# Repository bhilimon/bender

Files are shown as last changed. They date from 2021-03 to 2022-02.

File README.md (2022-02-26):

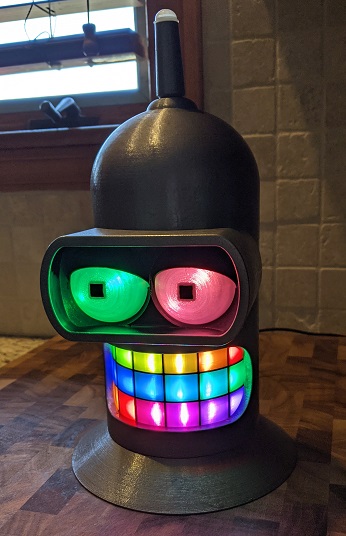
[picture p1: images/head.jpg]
Head


This is a talking Bender head from Futurama. It's controlled by a [Adafruit Feather RP2040](https://www.adafruit.com/product/4884) microcontroller and [CircuitPython](https://circuitpython.org/). The main features are:

* He talks! Plays random audio files at random intervals.
* He's colorful! 20 programmable NeoPixel LEDs that play various animations when talking and when idle.
* Antenna is also a motion detector that can trigger audio.
* Antenna is also a button to toggle modes (see below).

A quick video showing what it looks like: [https://youtu.be/TiZu5_Vf4qA](https://youtu.be/TiZu5_Vf4qA)

This project takes quite a bit of time to print, put together, and to gather and properly prep all your audio files. Make sure you read all the documentation about the issues I ran into and limitations before starting this project. 

[Thingiverse Page](https://www.thingiverse.com/thing:4816306)

## Images
See [images](https://github.com/bhilimon/bender/tree/main/images).

## Config Options
Configurable options include:
* Min/max wait times between playing random audio
* Motion detector wait timer (after playing audio)
* Min/max on changing eye colors
* Timer on changing teeth LED animations
* Initial / startup mode (see below)
* A basic config of every animation in the [CircuitPython LED animation library](https://circuitpython.readthedocs.io/projects/led-animation/en/latest/index.html) is included. You can easily modify them and enable/disable certain animations.

## Modes / Changing Modes
There are 3 modes, controlled by pushing the antenna down (it's also a button). Mode changes are indicated by momentarily lighting up 1, 2, or 3 teeth blue. Note: you can only change the mode while audio is not playing.
1. Audio on, motion detector on
2. Audio on, motion detector off
3. Audio off

## Parts List
* [Adafruit Feather RP2040](https://www.adafruit.com/product/4884)
  * Which microcontroller you use is flexible as long as it can support the inputs, outputs, CircuitPython, and the modules you need, mainly NeoPixels, audiobusio, and audiomixer. This project does not use any analog inputs or outputs. The main concern is storage space for audio files, which is extremely limited on microcontrollers. The Adafruit RP2040 boards have 8MB of flash for storing audio files. Adafruit is also working on adding MP3 audio support on their RP2040 boards which will help with the storage limits. If you use a different microcontroller you might have to adjust 3D models for mounting holes and alignment of the USB power cable hole on the back of the head.
* [Adafruit I2S Audio Amp](https://www.adafruit.com/product/3006)
  * See the audio notes / issues section below. Other amps will likely work, likely requiring wiring and code tweaks.
* [Adafruit Mini NeoPixels](https://www.adafruit.com/product/2959)
  * You will only need 20 NeoPixels but you _need_ ones with 0.66"/17mm spacing between LEDs to align properly with the teeth. You will not be able to mount NeoPixels with wider spacing.
  * I went with the "Mini" NeoPixels due to the lower power requirement to be sure I can power everything through the Feather. Even at 50% brightness they are plenty bright enough if you have pretty clear PLA for the teeth and eyes. Regular sized NeoPixels should work but have not been tested. They might draw too much power.
* [Adafruit Mini PIR Motion Sensor](https://www.adafruit.com/product/4871) 
* Speaker
  * You need a square 50mm (2 inch) 4-8ohm speaker. There is only about 52mm clearance for mounting. There are 3D models for both 40mm and 42mm mounting hole spacing since there doesn't seem to be a standard. An 8ohm speaker will use less power and is recommended.
* Power Supply
  * You need a USB-C power supply that can support 20 NeoPixels, the microcontroller, the amp, and a speaker. I don't exactly know how much power everything draws but I imagine 500-600mA should be plenty. I used the [official Raspberry Pi power supply](https://www.adafruit.com/product/4298) because it's cheap, small, and can provide more power than you'll need. The 20 NeoPixels alone can in theory pull 400mA (at 100% brightness and full white).
* PLA / Printing
  * You will need some clear/transparent/translucent PLA or other filament for printing the teeth and eyes so the LEDs can shine through. A small 50 gram spool of clear is plenty. The rest of the parts will need around 500 grams depending on how you print.
* Button
  * You need a small button to mount inside the antenna base. I just glued a basic 6mm x 6mm x 5mm (H) breadboard button. If you use a different size switch you might have to tweak the two 3D models for the antenna parts. There is a small amount of extra space around my button.

## Wiring Diagram
See [doc/wiring-diagram.png](https://github.com/bhilimon/bender/blob/main/doc/wiring-diagram.png)

## 3D Printing
See [doc/PRINTING.md](https://github.com/bhilimon/bender/blob/main/doc/PRINTING.md)

## Assembly
See [doc/ASSEMBLY.md](https://github.com/bhilimon/bender/blob/main/doc/ASSEMBLY.md), there's a few assembly [images](https://github.com/bhilimon/bender/tree/main/images) as well.

## Audio Files, Prep, and Issues
For copyright reasons no audio files are included. You'll have to find them online and convert them down to a low enough bitrate your microcontroller can support and to small enough file sizes for the flash storage limitations of the microcontroller. You can use [this guide](https://learn.adafruit.com/microcontroller-compatible-audio-file-conversion) to convert your files. 

I use 11025 Hz, 16 bit, mono audio files which works good. I have some weird audio chirping / noise when using 22050 Hz audio files. I don't know why, but going down to 11025 Hz works fine and there is no noticeable loss of quality.

## Other Notes / Limitations
 * The teeth and eyes are separate NeoPixel chains since I don't want the eyes included in the animations. This can easily be changed by changing wiring and code. 
 * I was originally planning to make my own LED animations but once I found the CircuitPython LED animation library I ended up just using it since it has plenty of variety. Integrating your own custom animations will be tough since I use the AnimationSequence() class. I briefly pause the animation sequence while audio is playing to show the special "talking" animation, then resume it when audio is done.
 * Remember this is a microcontroller with not much storage space. You'll only be able to store a couple minutes of audio, total. 
 
## Credits
The original idea and 3D model came from [another project](https://www.thingiverse.com/thing:4384974). I completely changed the electronics and code to run from a microcontroller instead of a Raspberry Pi. I've made some various changes to the some 3D models to support my hardware and project changes. The original files as well as updated files are all available as well as the editable sources if you need to tweak things.

## Change Log
2/26/2022
 * Removed workarounds for audio playback issues that were fixed in CircuitPython 7.
 * Added audiomixer module as a method to control volume, which also came in CircuitPython 7.

4/5/2021
 * Initial rev

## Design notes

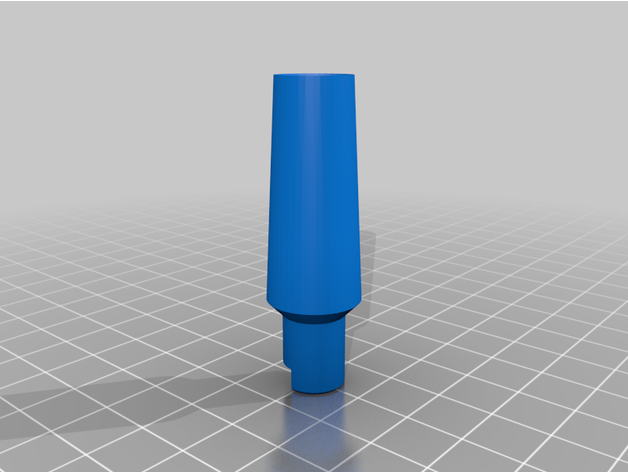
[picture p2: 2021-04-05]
images/renderings/featured_preview_bndr-antennanew.png

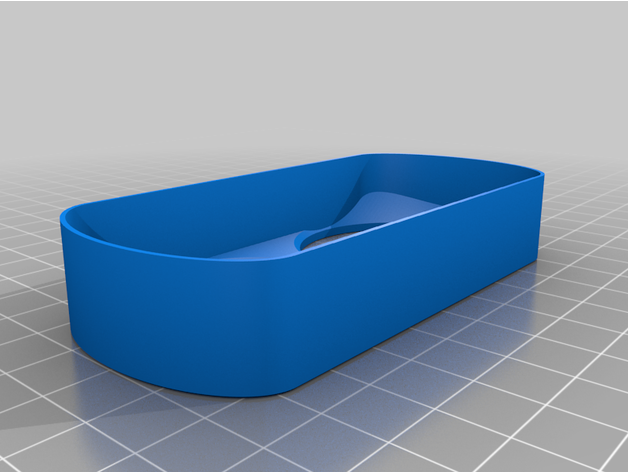
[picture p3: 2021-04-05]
images/renderings/featured_preview_bndr-visor-front.png

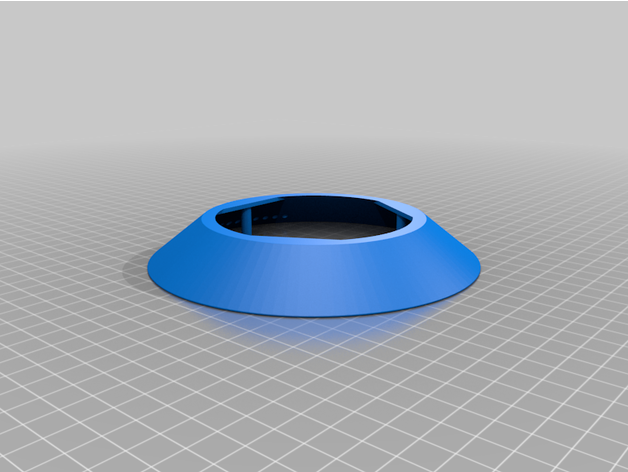
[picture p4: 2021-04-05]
images/renderings/featured_preview_benderbase.png

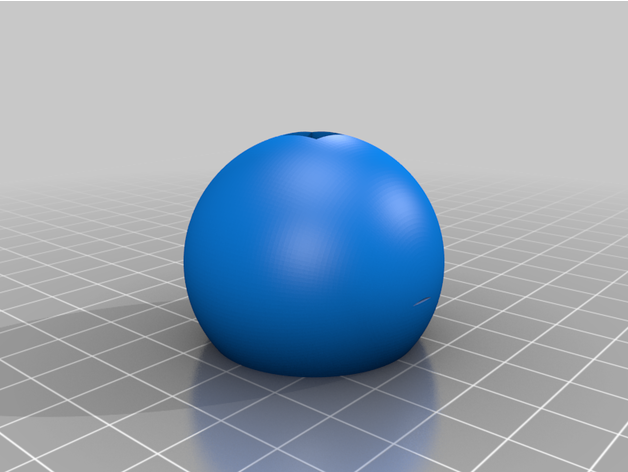
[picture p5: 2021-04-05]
images/renderings/featured_preview_bndr-eye.png

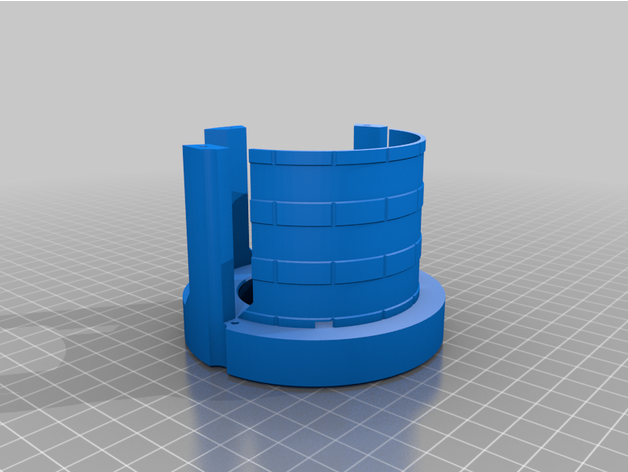
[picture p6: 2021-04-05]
images/renderings/featured_preview_bndr-inner-bottom-40mmnew.png

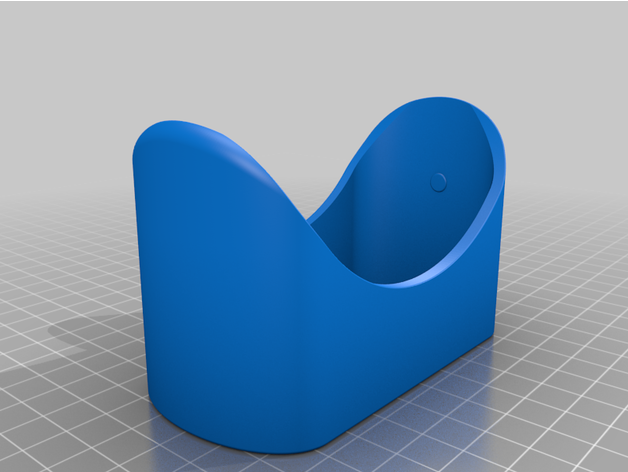
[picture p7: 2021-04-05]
images/renderings/featured_preview_bndr-visor-shell.png

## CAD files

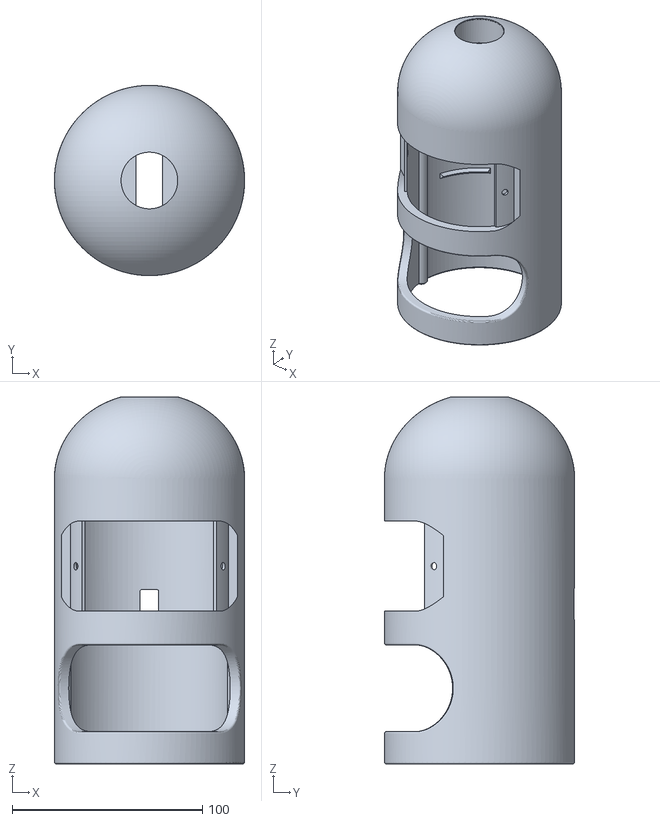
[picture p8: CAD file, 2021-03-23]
models/new-body-complete.stl
100.0 x 100.0 x 192.9

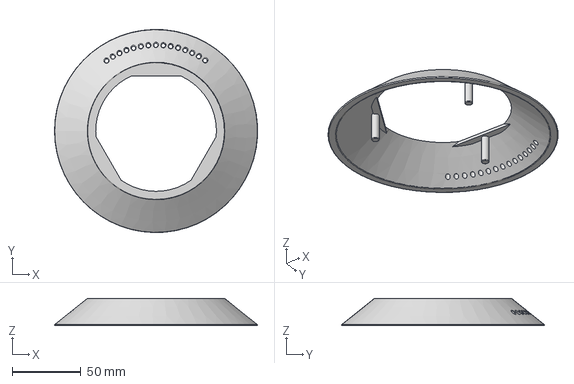
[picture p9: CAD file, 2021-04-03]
models/benderbase.step
148.0 x 148.1 x 20.0 mm

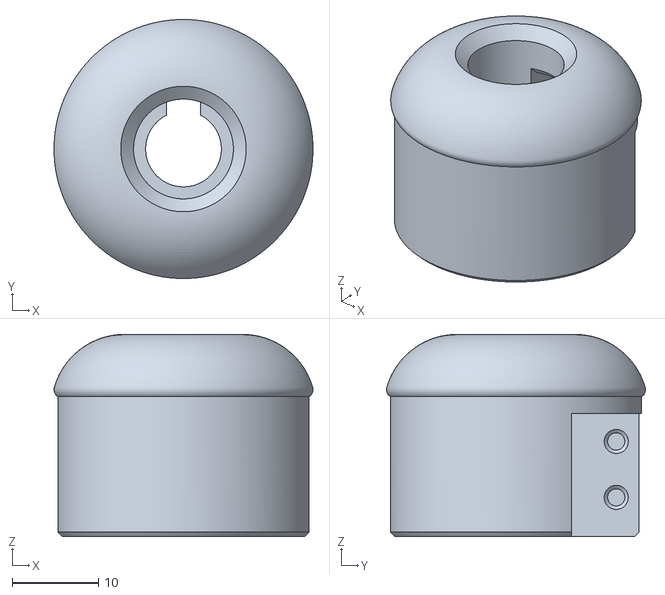
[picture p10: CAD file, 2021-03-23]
models/original/bndr-antenna-base.stl
30.1 x 30.1 x 23.5

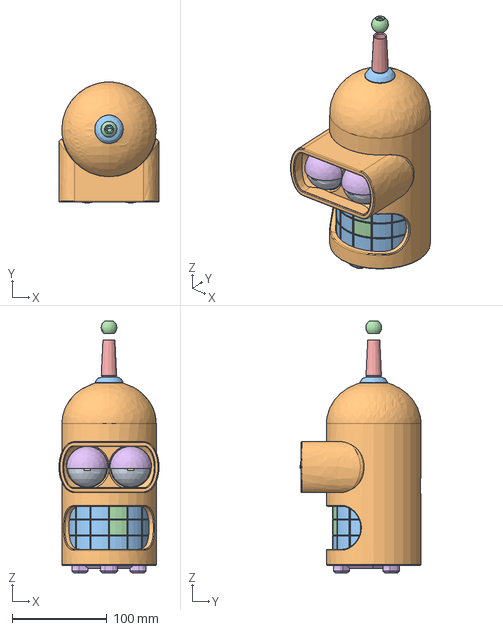
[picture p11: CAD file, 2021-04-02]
models/bender.step
105.9 x 128.0 x 266.6 mm

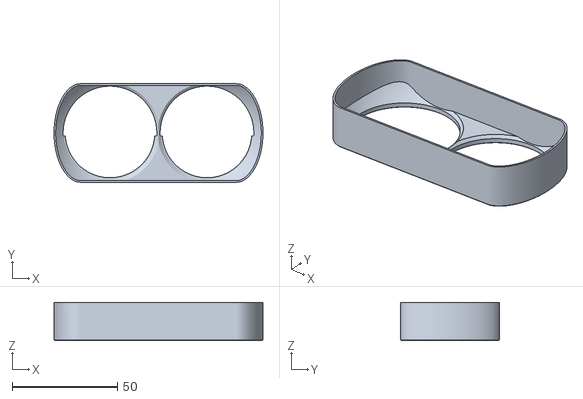
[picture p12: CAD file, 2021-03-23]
models/original/bndr-visor-front.stl
99.1 x 46.7 x 18.2

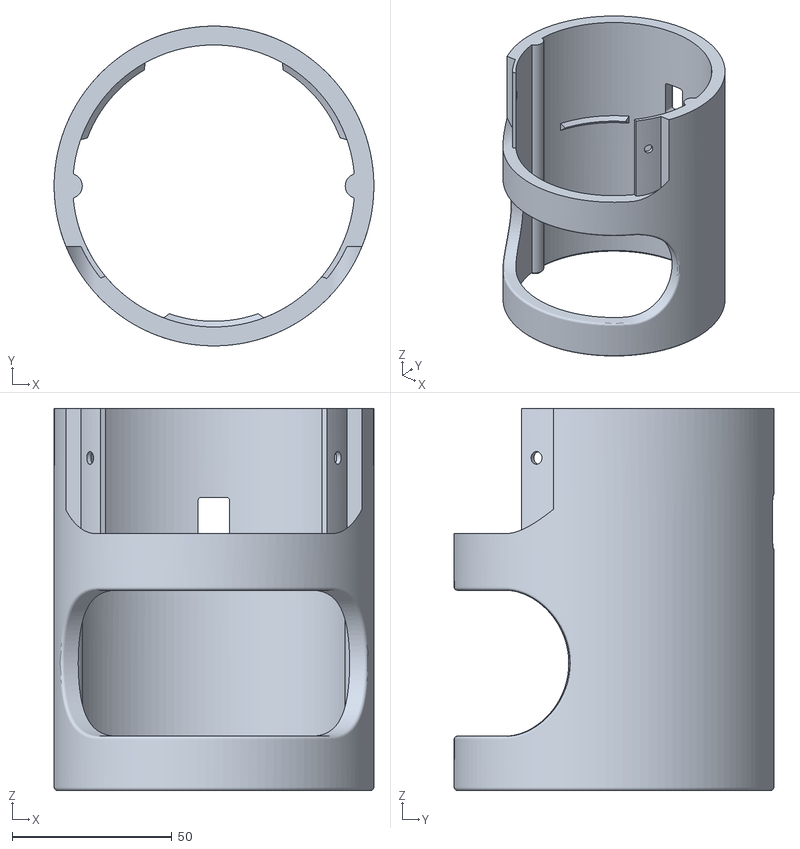
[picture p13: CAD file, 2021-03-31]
models/new-body-bottom.stl
100.0 x 100.0 x 119.5

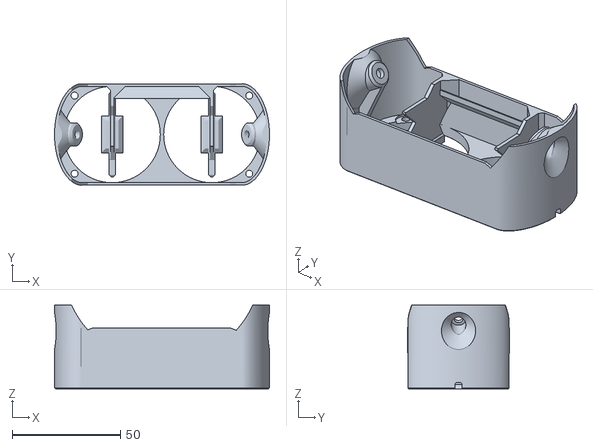
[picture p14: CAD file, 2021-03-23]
models/original/bndr-visor-inner.stl
99.1 x 46.8 x 38.5

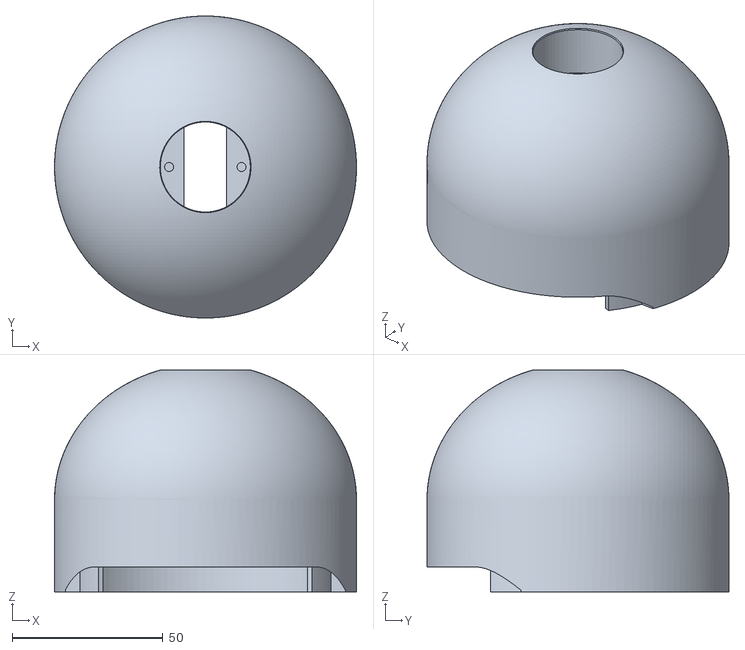
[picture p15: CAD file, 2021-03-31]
models/new-body-top.stl
100.0 x 100.0 x 73.4

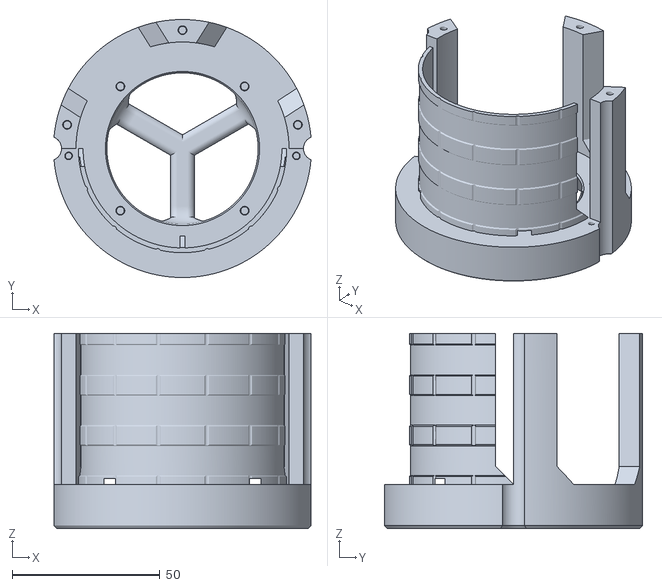
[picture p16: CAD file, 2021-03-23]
models/original/bndr-inner-bottom.stl
86.9 x 87.2 x 66.0

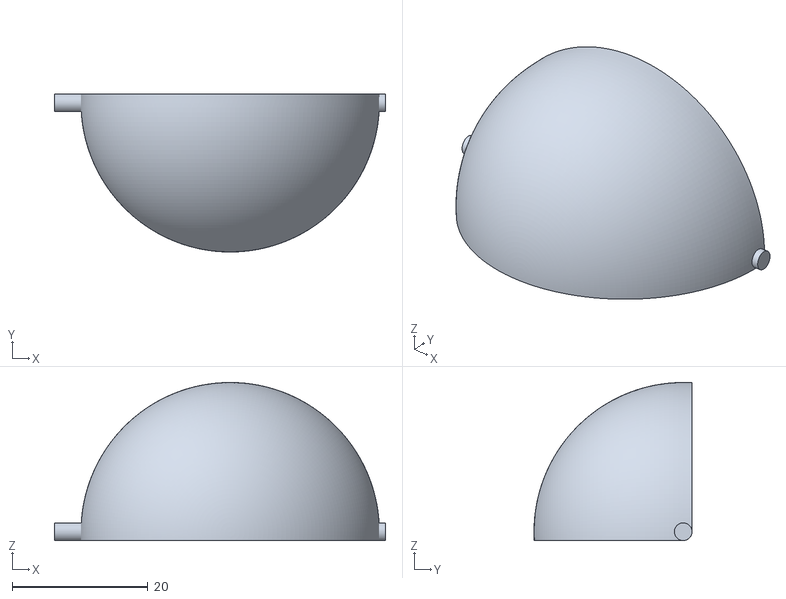
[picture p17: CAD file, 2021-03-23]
models/original/bndr-eyelid-right.stl
48.8 x 23.3 x 23.3

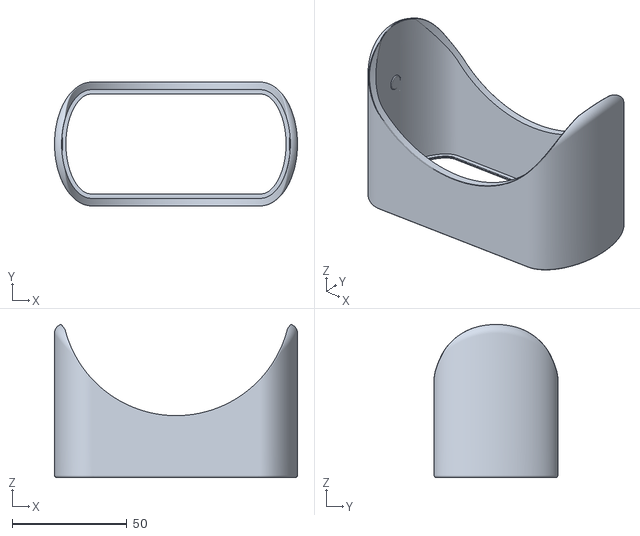
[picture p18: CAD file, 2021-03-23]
models/bndr-visor-shell.stl
105.9 x 54.0 x 66.7

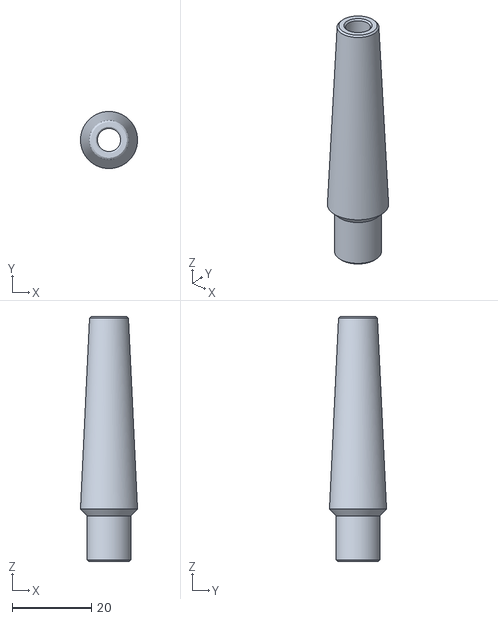
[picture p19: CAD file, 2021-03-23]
models/original/bndr-antenna-stem.stl
14.4 x 14.4 x 61.8

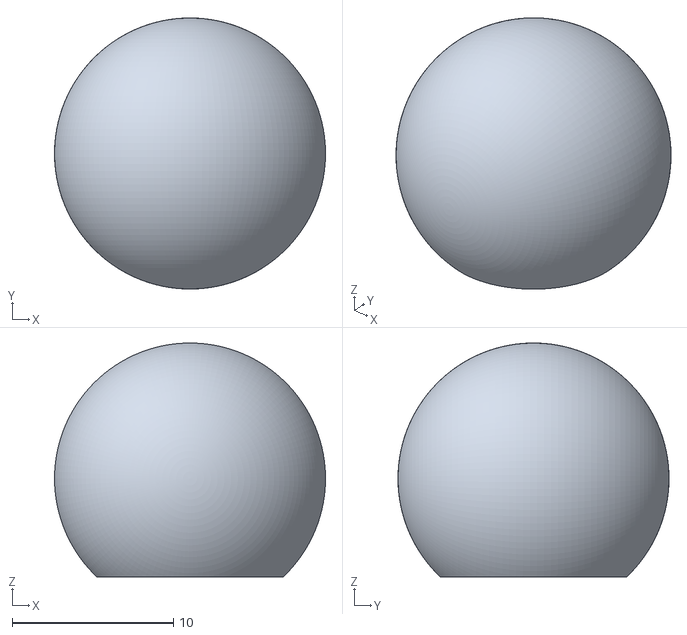
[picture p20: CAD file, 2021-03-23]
models/original/bndr-antenna-top-B.stl
16.8 x 16.8 x 14.5

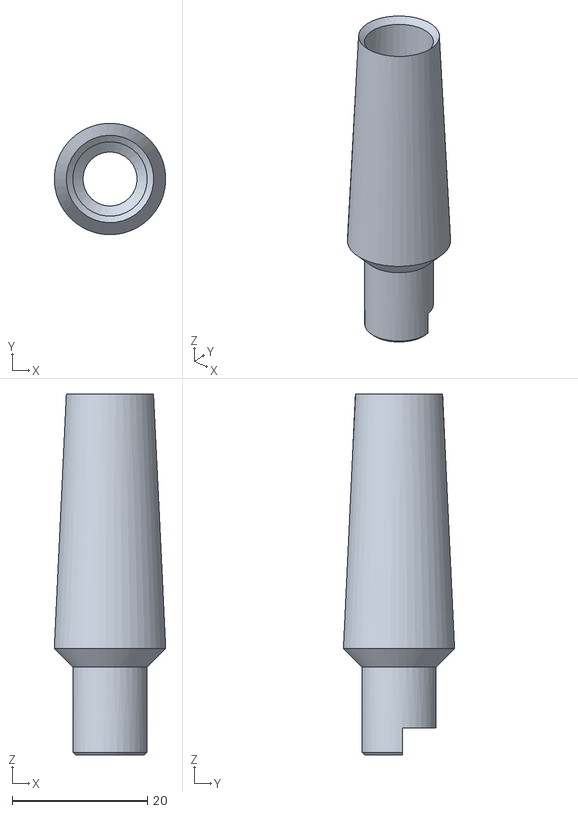
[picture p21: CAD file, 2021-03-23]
models/bndr-antenna(new).stl
16.5 x 16.4 x 53.4

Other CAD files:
models/bndr-eyelid-left.stl
models/original/bndr-antenna-top-A.stl
models/bndr-antenna-base(new).stl
models/bender.f3d
models/benderbase.f3d
models/benderbase.stl
models/bndr-eye.stl
models/bndr-feet.stl
models/bndr-inner-bottom-40mm(new).stl
models/bndr-inner-top(new).stl
models/bndr-pupil.stl
models/bndr-teeth-mount.stl
models/bndr-tooth.stl
models/original/bender.stp
models/original/bndr-eye-x2-SLA.stl
models/original/bndr-eyelid-left.stl
models/original/bndr-feet.stl
models/original/bndr-inner-pimount.stl

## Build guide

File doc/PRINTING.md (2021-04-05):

Lots of parts to print. I've noted the colors you should print if you don't plan on painting anything. Model files with "new" in the file name means I changed something from the original source model. The Fusion 360 & STEP files are included if you need to modify anything but my changes from the original model are sort of hacked together in it.

### Teeth
* Print 18 teeth from "bndr-tooth.stl"
* Color: clear

### Teeth Mounts
* Print 3 teeth mounts from "bndr-teeth-mount.stl"
* Color: black

### Inside Top
* Print "bndr-inner-top(new).stl"
* Color: any (not visible)

### Inside Bottom
* Print "bndr-inner-bottom-42mm.stl" if your speaker mounting hole spacing is 42mm
* Print "bndr-inner-bottom-40mm(new).stl" if your speaker mounting hole spacing is 40mm
* Color: any (not visible)

### Feet
* Print "bndr-feet.stl"
* Color: gray or black
* Note: print the feet even if you plan on using the optional flared base / neck. They help hold it in place.

### Eyes
* Print 2 "bndr-eye.stl"
* Color: clear

### Eyelids
* Print "bndr-eyelid-left.stl"
* Print "bndr-eyelid-right.stl"
* Color: black

### Pupils
* Print 2 "bndr-pupil.stl"
* Color: black

### Visor Outer Shell
* Print "bndr-visor-shell.stl"
* Color: gray

### Visor Inner
* Print "bndr-visor-inner.stl"
* Color: black

### Visor Inner Front
* Print "bndr-visor-front.stl"
* Color: black

### Antenna
* Print "bndr-antenna(new).stl"
* Color: gray

### Antenna Base
* Print "bndr-antenna-base(new).stl
* Color: gray

### Body
* Print "new-body-complete.stl" if you want a single body (long print)
* Print "new-body-top.stl" and "new-body-bottom.stl" if you want a 2 part body to break up the printing time.
* Color: gray

### Base (optional)
* Print "benderbase.stl" if you want the flared base / neck. This is optional. He will stand without it.
* Color: gray

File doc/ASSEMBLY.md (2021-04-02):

General assembly guide. Be sure you leave enough wire so you're able to remove the visor and inside.

### NeoPixels
1. You need (3) 6-NeoPixels chained together for the teeth sections for a total of 18 NeoPixels.
2. You need (2) single NeoPixel segments chained together for the eyes.

### Inside / Bottom Assembly
1. Attach feet to inner-bottom with (3) M3-4mm screws.
2. Attach speaker with (4) M3-4mm screws.
3. Slide teeth into the teeth mounts.
4. Glue the 3 teeth mount sections together.
5. Install NeoPixels behind the teeth and attach teeth assembly to the inner base.
  * It's up to you what direction you want to mount the strips. I went bottom-to-top, left-to-right, as if I was facing the head. It just depends on how you want the animations to flow.
  * This step is a pain. I managed to do it without any glue after some frustration.
6. Attach the inner-top with (3) M3-4mm screws to hold together the complete inside assembly.

### Visor / Eyes Assembly
1. Attach NeoPixels to the 2 mounting pads on the inner-visor.
2. Glue the pupils to the eyes (from the inside).
2. Connect eyes to the mounting points above and below the NeoPixels.
3. Slide eyelids in.
4. Secure everything by attaching the outer-visor with (4) M3-4mm screws.

### Antenna
1. Wire motion detector and install in antenna. It's a firm fit but should snap in.
2. Wire the mode button and install (glue) it in the antenna base. The edge of the antenna should rest on the button so it can push it. Be sure to verify button placement before you glue.
3. Attach antenna base to head with (2) M3-4mm screws.

### Last Steps
1. Install controller and amp with (3) M2 screws.
2. Wire everything up.
3. Slide in the inside assembly.
4. Slide in the visor assembly, attach with (2) M3-10mm (or longer) screws.
5. Slide on the visor cover.
